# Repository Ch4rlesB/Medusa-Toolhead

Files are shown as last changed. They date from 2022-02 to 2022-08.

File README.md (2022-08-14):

# Medusa-Toolhead
**__IN BETA 3__**
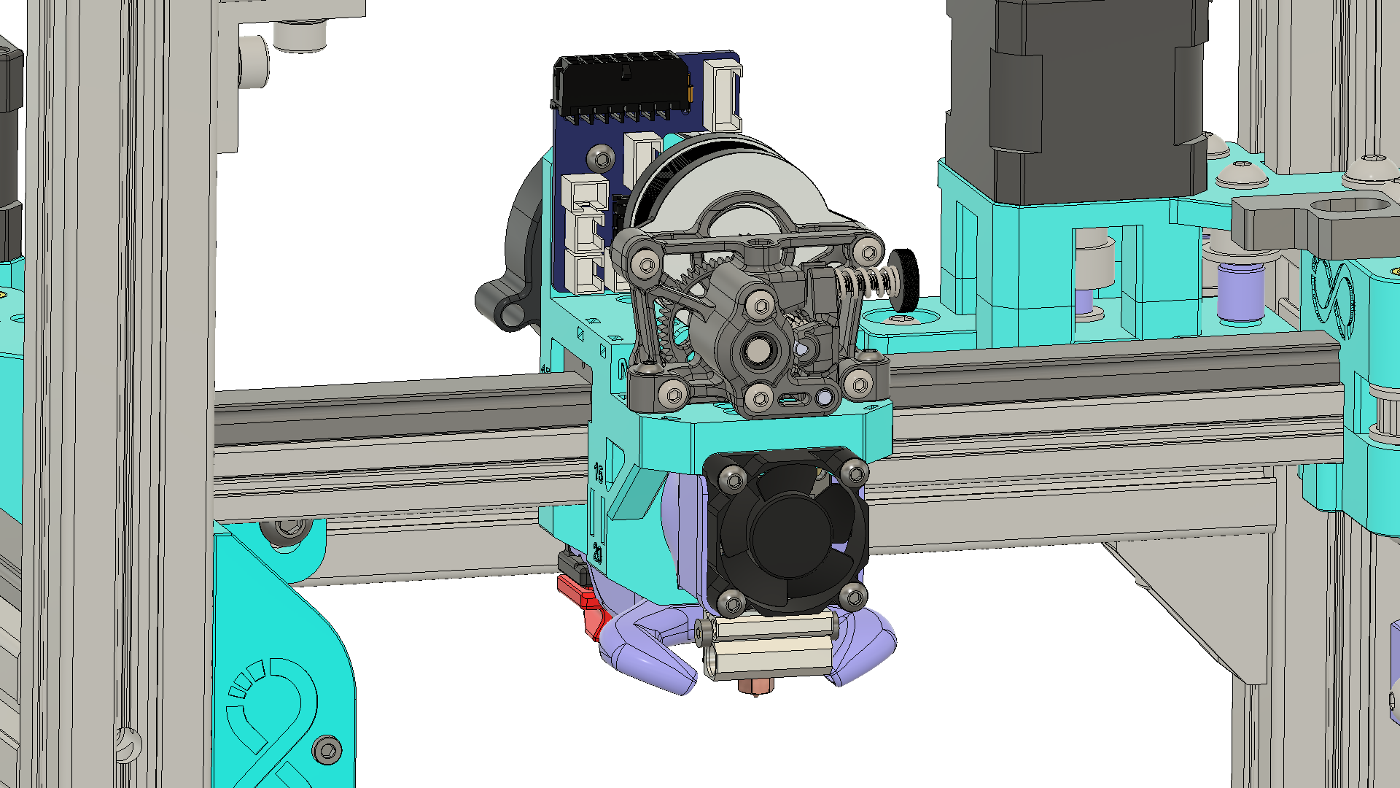
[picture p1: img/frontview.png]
FrontView


**Beta 3 Changelog:**
- Removed the slide in belt attachment method. You now loop around a post and ziptie the belt to itself, à la VZBot. (Pardon my french)

- Much Much MUCH stiffer. Horizontal bar that holds extruder and hotend does not flex at all now.

- Removed compability for the BLTouch as it is too unreliable inside a 60C enclosure.

- Narrowed down the Umbilical options to:

	I. Straight umbilical with strain relief.

	II. Hartk Afterburner Toolhead board. (ALOT of different wiring            harnesses on aliexpress made to work with this board that                facilitate 		   wiring overall)

- Standardized the screw sizes.

- CFD work to align the airflow from the duct better.

# **__What is it?__**

EVA 2.4 replacement for the [**SnakeOil-XY CoreXY 3D Printer**](https://github.com/ChipCE/SnakeOil-XY).

Designed to need the least hardware possible while still being stiff and light.

## **1. Toolhead**

### 1.1 Currently supports:

	Extruder:
	-Sherpa Mini Extruder
	
	Hotend:
	- Dragon SF and HF
	- Mosquito or NF-Crazy
	
	Probe:
	- Klicky Probe

	Umbilical:
	- Hartk Voron 2.4 Toolhead board
	- Normal umbilical
  Toolhead Board            |  No Toolhead Board
:-------------------------:|:-------------------------:
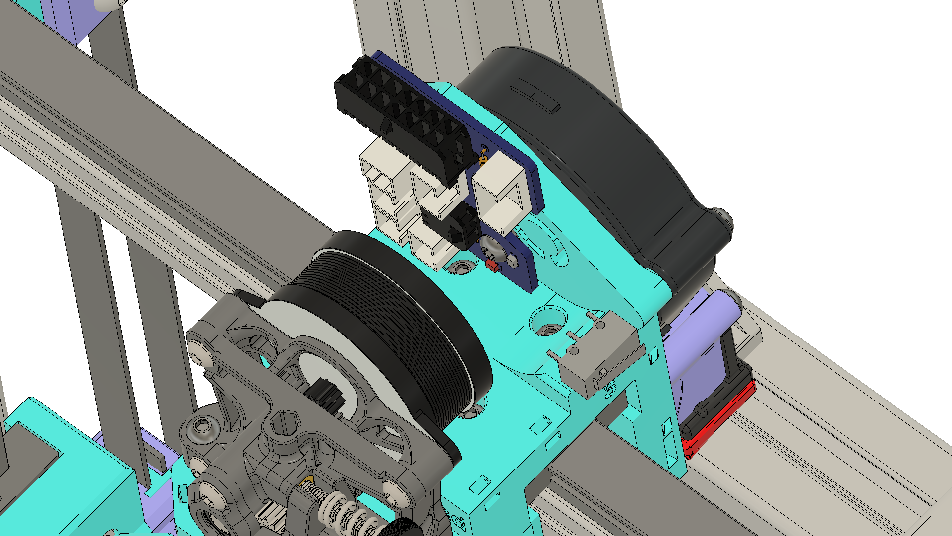
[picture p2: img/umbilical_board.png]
umbilical_board
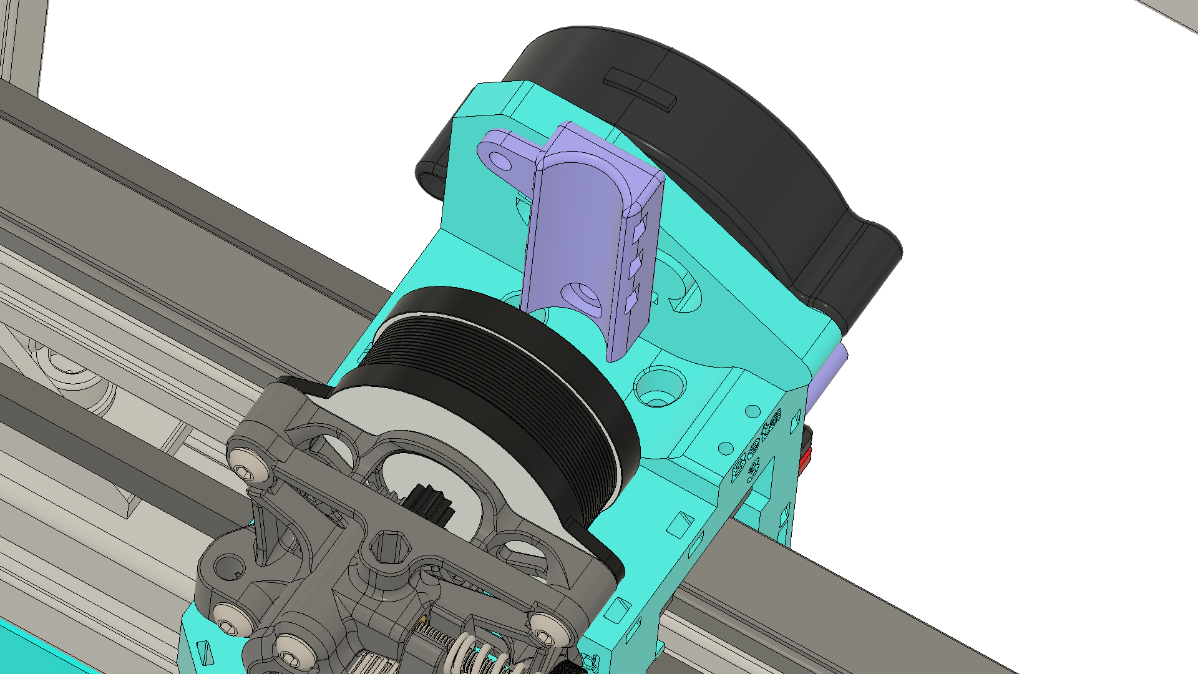
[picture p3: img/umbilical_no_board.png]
umbilical_no_board
  |  

### 1.2 Cooling 
Uses a modified [Eva](https://github.com/EVA-3D/eva-main) cooling duct.
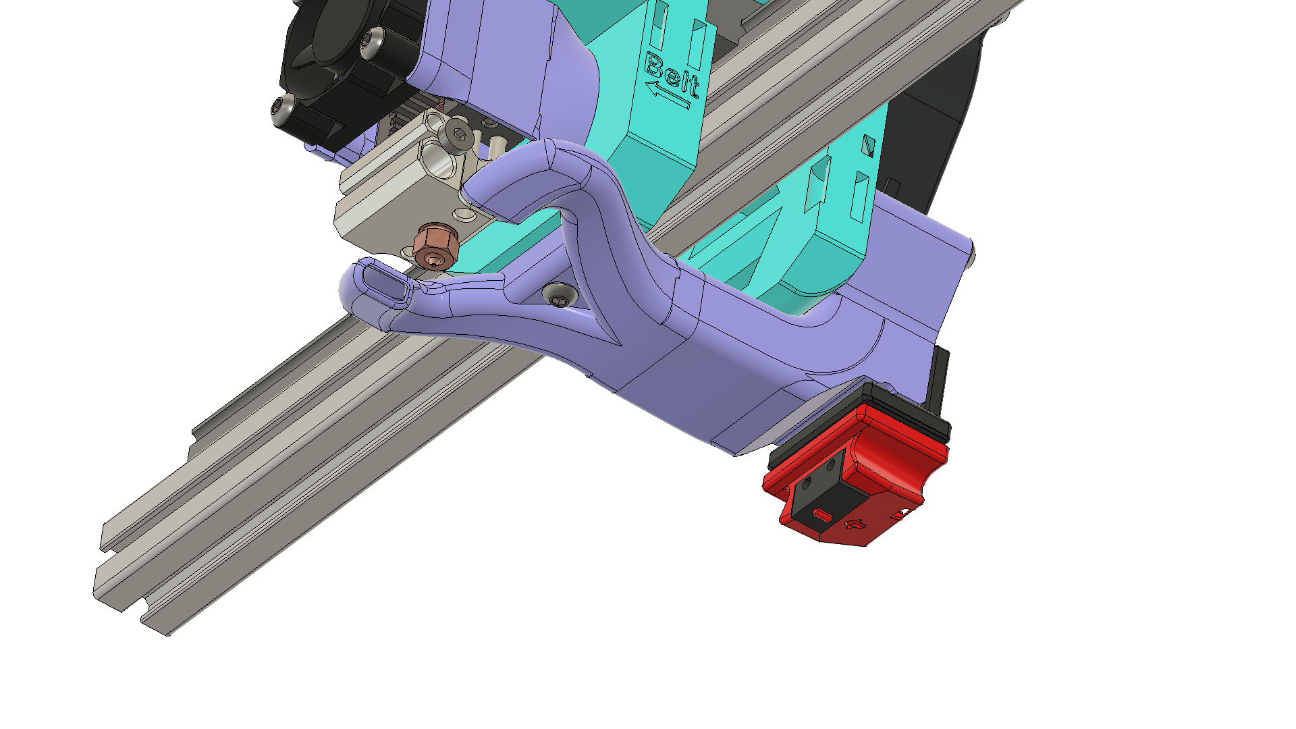
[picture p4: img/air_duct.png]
Air Duct

### 1.3 Offsets
	 x : -1.8 mm
	 y : 76.85 mm
	 z : 6.2 mm
### 1.4 BOM
	- 1x Dragon OR Mosquito (NF-Crazy) Hotend

	- 1x Fully Assembled Sherpa Mini Extruder

	- 1x 3010 Fan for hotend cooling.
	
	- 1x 5015 Fan for part cooling

	- 6x M3-6mm Screw (MGN12, Umbilical)

	- 7x M3-12mm Screw (Hotend Cooling Fan, Shroud, Cooling Duct, Sherpa mini mounting)

	- 3x M3-25mm Screw (Cooling Duct and Fan) 

	- Mounting hardware that goes with your hotend (Usually 2 or 4 M2.5 screws)

	- 2x M2x10mm self tapping screws (Endstop mounting)

	- 14x M3 Heatset insert M3x4mmx4mm

	- OPTIONAL 1x hartk afterburner toolhead board

	- 4x Zipties (Belts)
						AND
	- Klicky
		- 2x M3-6mm Screw
		- 2x M3-16mm Screws
		- 2x M2-10mm self tapping screws
		- 2x M6-8mm Screw
		- 2x M3 Heatset insert M3x4mmx4mm
		- 1x Omron D2F Microswitch or similar
		- 8x 6x3mm round magnets
		
### Assembly

ToolheadAssembly

## **2. Tensioning Idlers**

Belt mounting on the toolhead itself is very simplified to save weight. You will need to print the tensioning front idlers and replace the static stock ones. This will allow you to tension the belts.

Front            |  Back
:-------------------------:|:-------------------------:
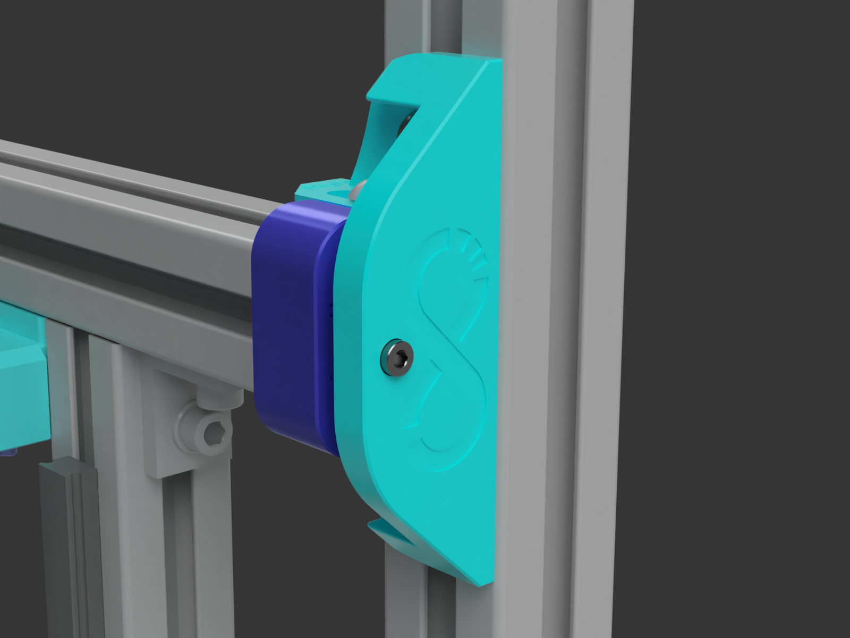
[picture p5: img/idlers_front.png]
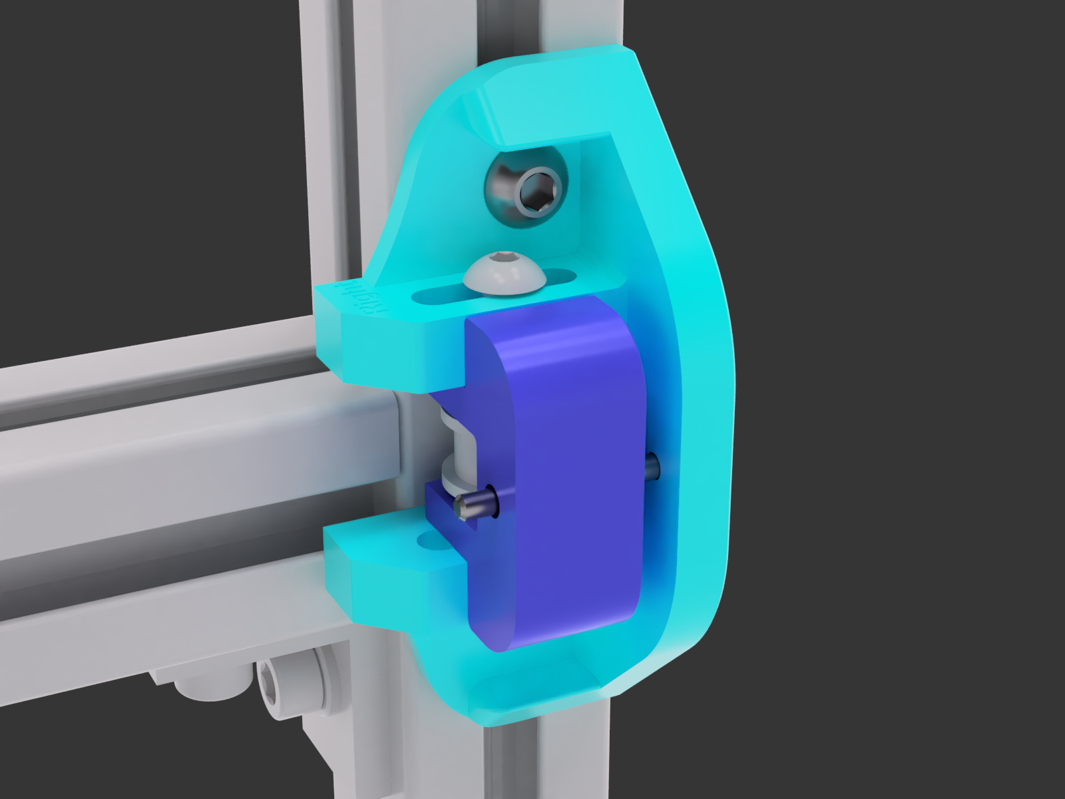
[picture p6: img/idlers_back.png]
  |  

### Bom
	- 2x M5x40mm Button Head (Idler shaft)
	- 2x M5 Standard Nut (Idler shaft)
	- 4x M6x8mm (Mouting the idlers to the frame - Reuse the ones used to hold the old idlers in place)
	- 2x M3x30mm Button Head (Tensioning Screw)
	- 12x M3 Heatset insert M3x4mmx4mm

## **3. Klicky Probe**
 Currently supports [Klicky probe](https://github.com/jlas1/Klicky-Probe) with a custom toolhead mount and dock mount.

Toolhead Mount            |  Dock & Mount
:-------------------------:|:-------------------------:
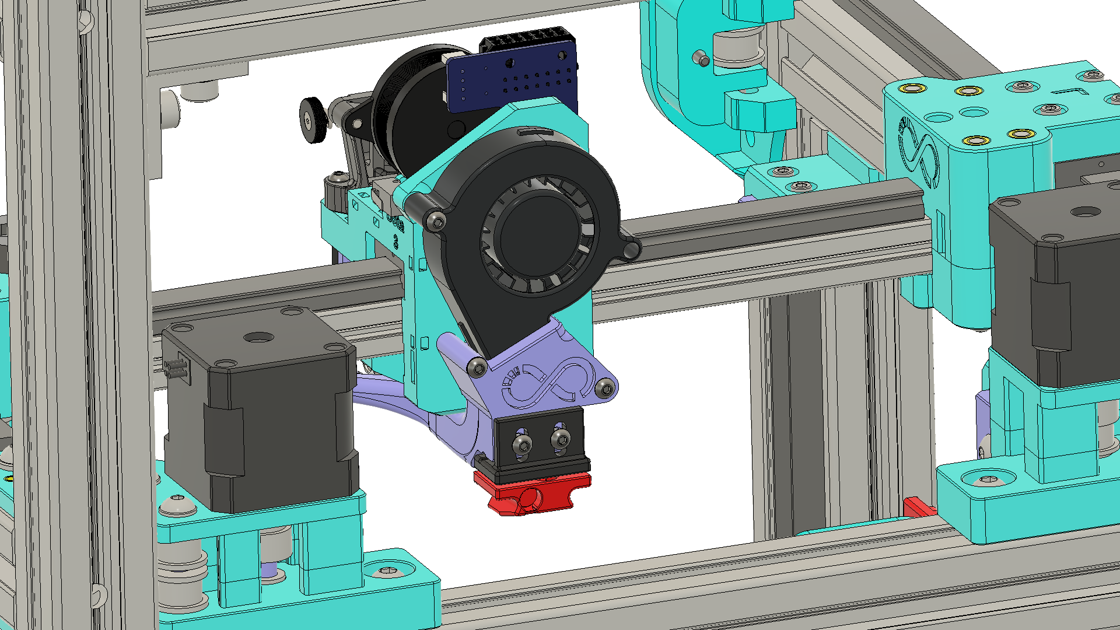
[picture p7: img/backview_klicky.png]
backview_klicky
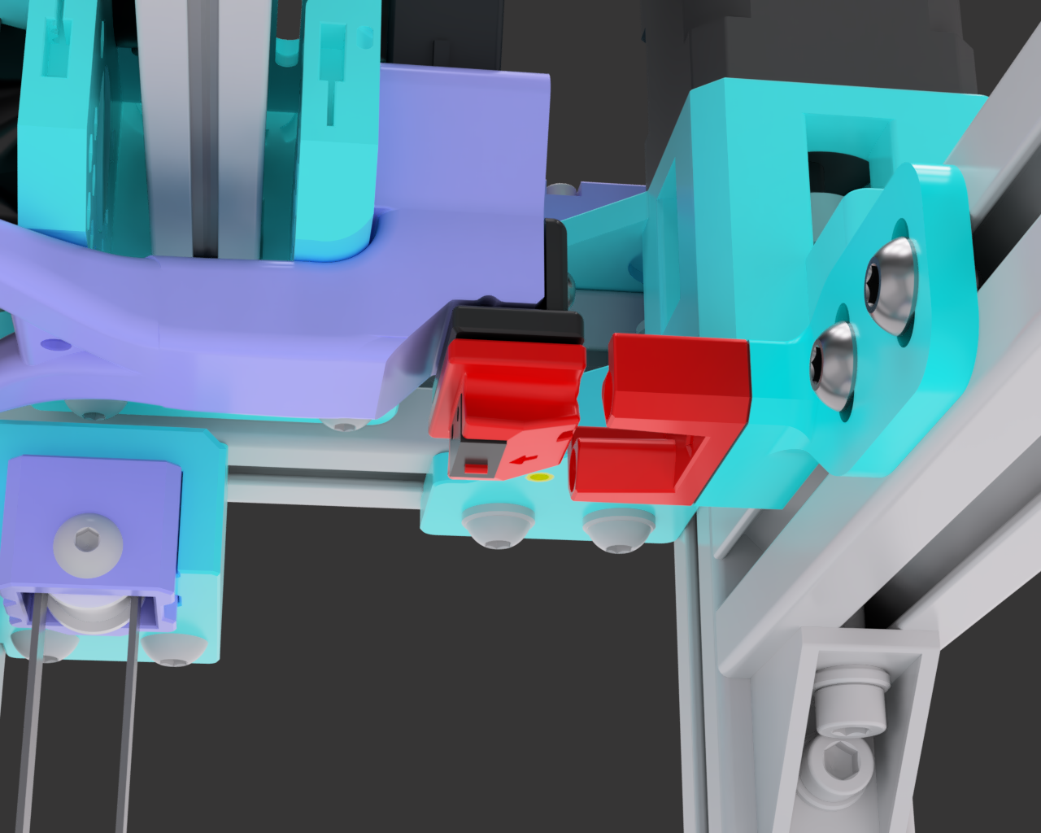
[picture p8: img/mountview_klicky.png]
mount_klicky
  |  

## **4. Z Endstop**
 Based on the Z endstop present on [Voron 3D Printers](https://github.com/VoronDesign).

 Acts as your z endstop and lets you use the [Z Calibration tool](https://github.com/protoloft/klipper_z_calibration) in conjunction with the Klicky Probe, to automatically set your Z offset independently of nozzle or print surface.

SnakeOil modified version            |  Based on the [Voron](https://docs.vorondesign.com/community/howto/120decibell/z_endstop_configuration.html) z endstop
:-------------------------:|:-------------------------:
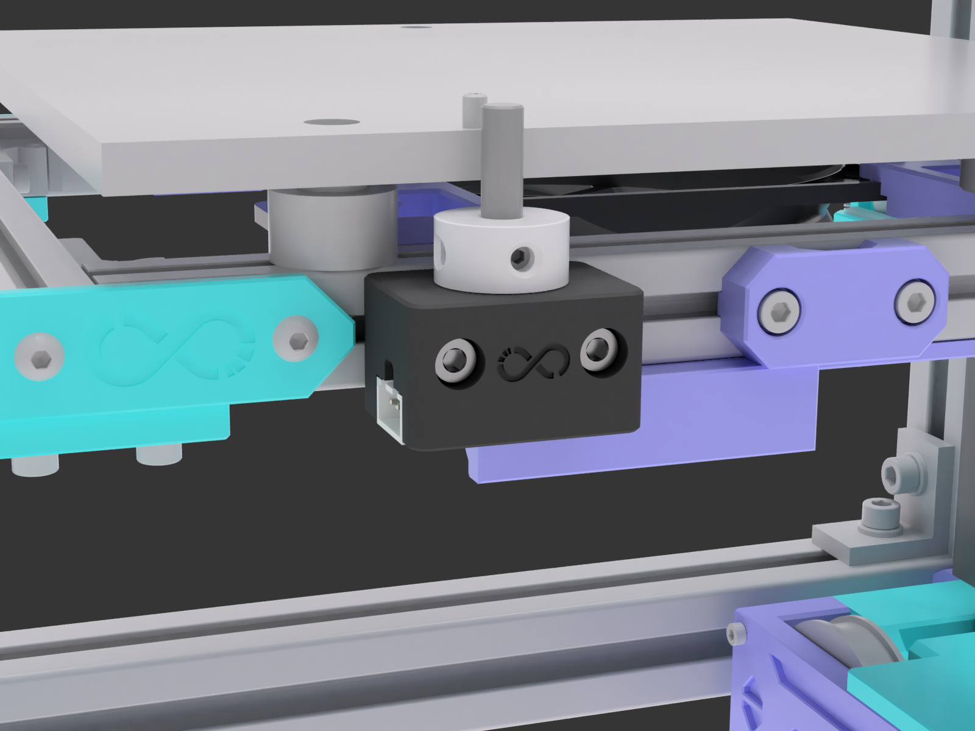
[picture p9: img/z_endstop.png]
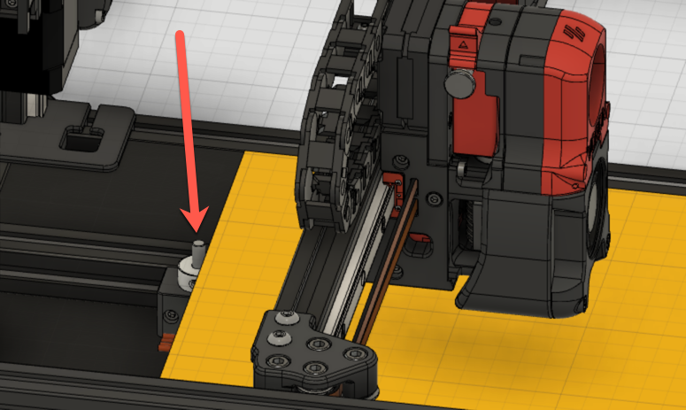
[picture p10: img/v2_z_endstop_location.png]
  |  

### Bom
	-2x M3x2mm Button Head (Mounting to bed)
	-2x M3 Standard Nut (Mounting to bed)
	-1x 5mm x 25mm Steel shaft
	-1x Omron D2F Microswitch or similar
	-1x 20-tooth timing pulley (deflanged)

 If you are having trouble taking the flange off the pulley visit the [version 2.2](https://github.com/VoronDesign/Voron-2/tree/Voron2.2/STLs/VORON2.2/Tools) of the Voron repository under tools. After printing out the hub puller and using the bolts from the kit, de-flanging is very easy.

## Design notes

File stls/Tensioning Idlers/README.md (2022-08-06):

If the part has this at the end of its name:
- <code> _1 </code> -> print 1

- <code> _a </code> -> print with your accent color

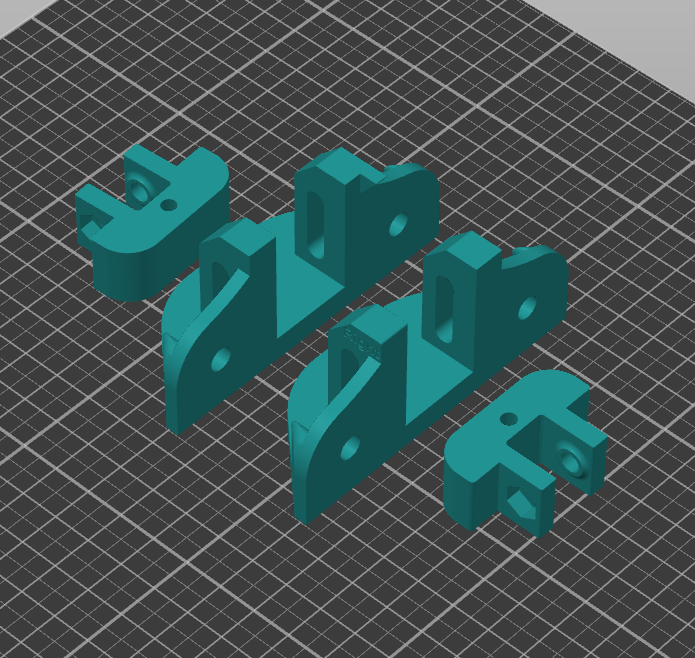
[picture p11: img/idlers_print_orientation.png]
PrintOrientation


When installing, make sure the idlers are at right height to keep belts parallel.

	- No need for support. 
	- 3-4 Perimeters
	- 30-40% Infill

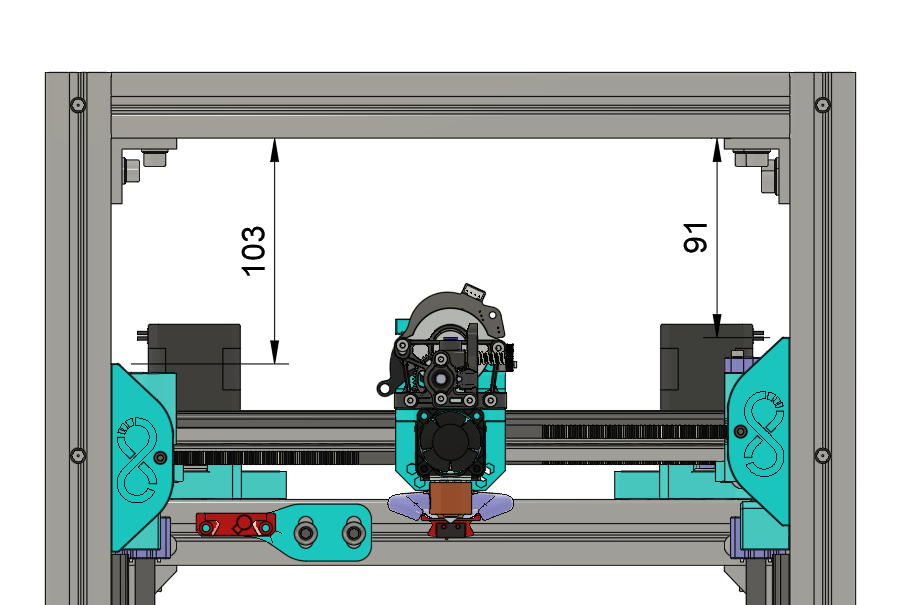
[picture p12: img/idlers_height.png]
IdlersHeight


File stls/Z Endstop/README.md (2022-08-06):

If the part has this at the end of its name:
- <code> _1 </code> -> print 1

- <code> _a </code> -> print with your accent color

	- No need for support. 
	- 3-4 Perimeters
	- 30-40% Infill

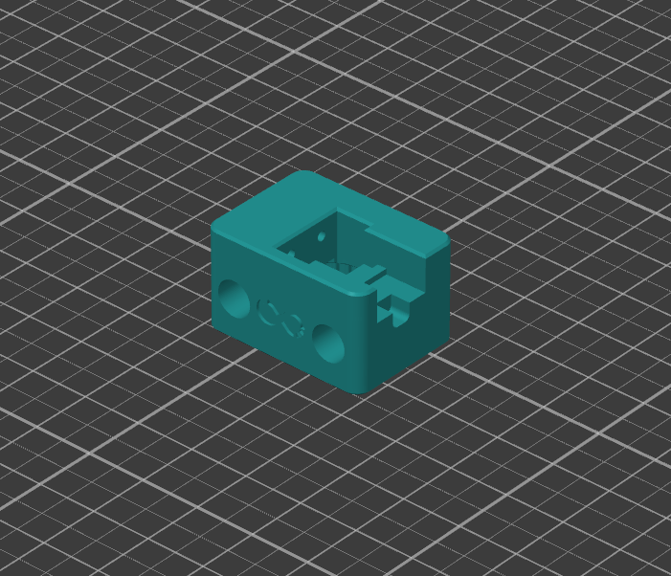
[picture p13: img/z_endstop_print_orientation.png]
PrintOrientation


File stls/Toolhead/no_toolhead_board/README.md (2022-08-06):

If the part has this at the end of its name:
- <code> _1 </code> -> print 1

- <code> _2 </code> -> print 2

- <code> _a </code> -> print with your accent color

	- No need for support. 
	- 3-4 Perimeters
	- 30-40% Infill

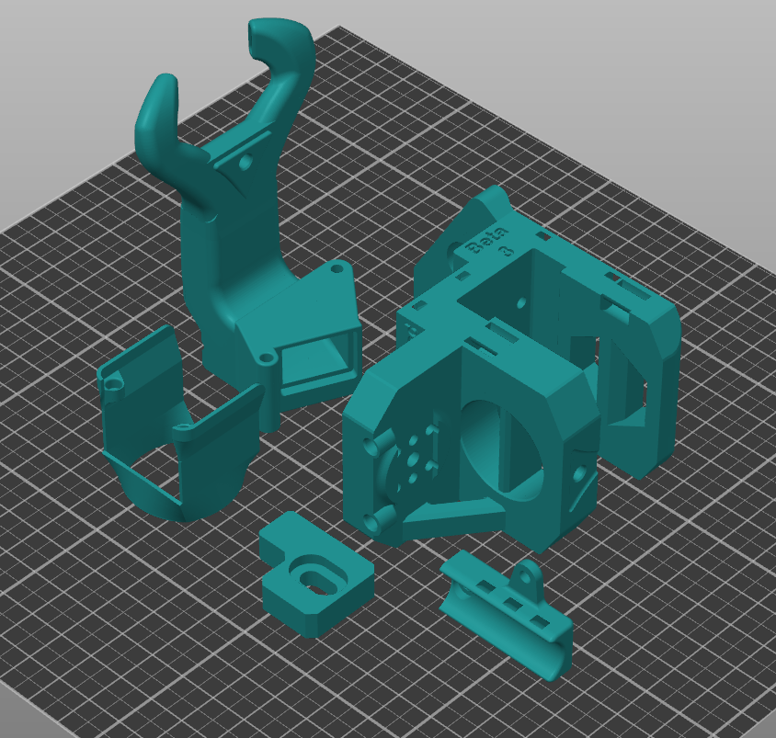
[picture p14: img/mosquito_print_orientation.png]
PrintOrientation


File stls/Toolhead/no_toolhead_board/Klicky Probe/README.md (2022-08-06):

If the part has this at the end of its name:
- <code> _1 </code> -> print 1

- <code> _2 </code> -> print 2

- <code> _a </code> -> print with your accent color

	- No need for support. 
	- 3-4 Perimeters
	- 30-40% Infill

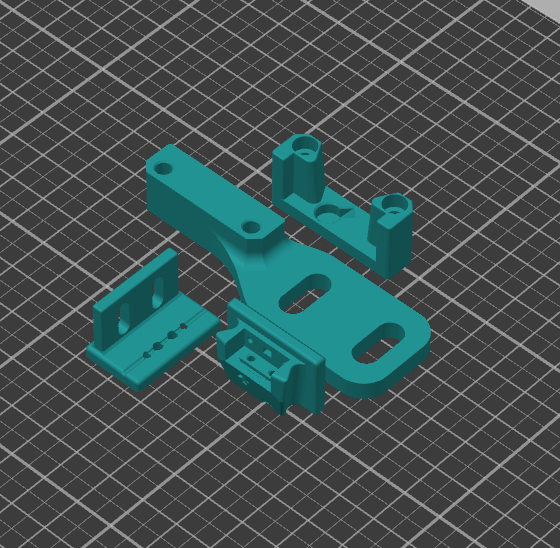
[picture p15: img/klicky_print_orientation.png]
PrintOrientation


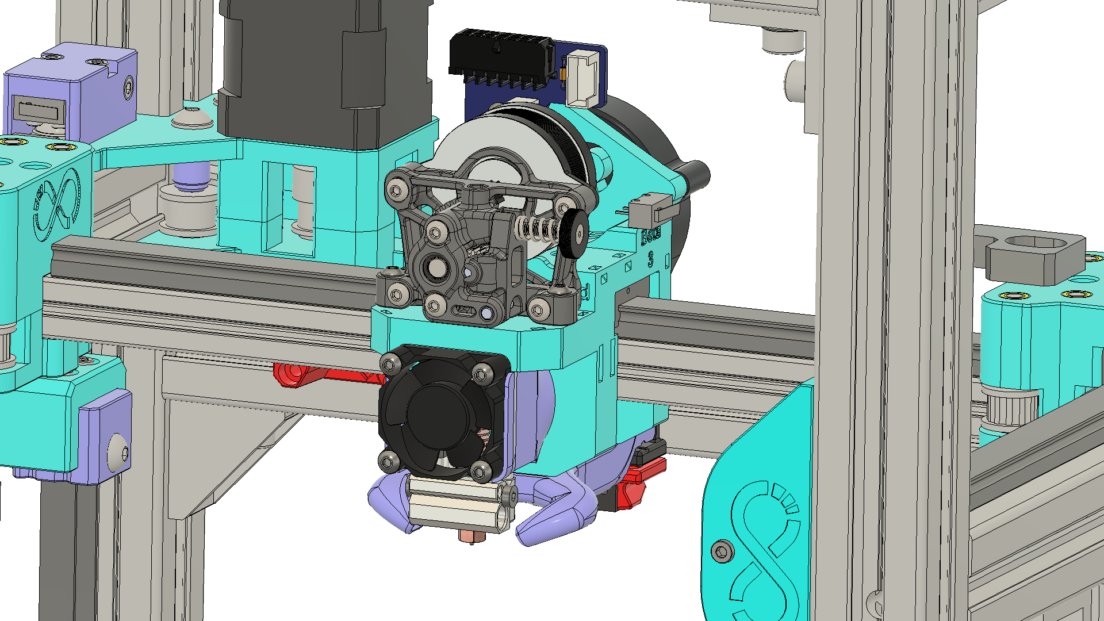
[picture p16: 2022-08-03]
img/frontview_klicky.png

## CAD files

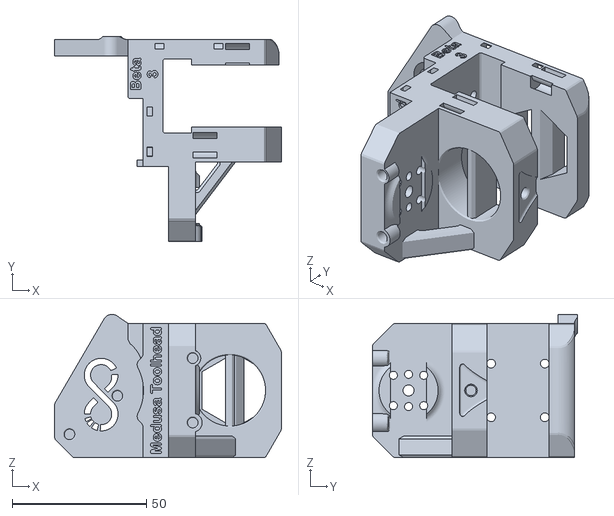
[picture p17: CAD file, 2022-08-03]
stls/Toolhead/no_toolhead_board/main_body_1.stl
84.6 x 76.5 x 53.3

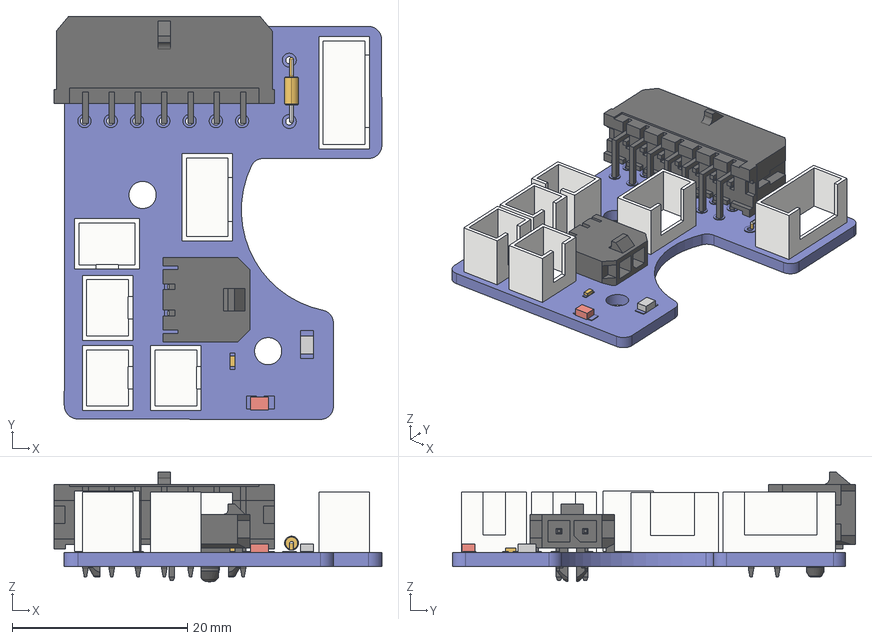
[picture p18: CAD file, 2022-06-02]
CAD/reference models/Toolhead pcb V2.4.step
37.4 x 46.0 x 12.5 mm
PCB (1)
CHAMBER THERMISTOR
RESISTOR
LED
ABL
STEPPER
XENDSTOP
BAT85
HEFAN
PCFAN
TH1
Microfit14
Microfit2

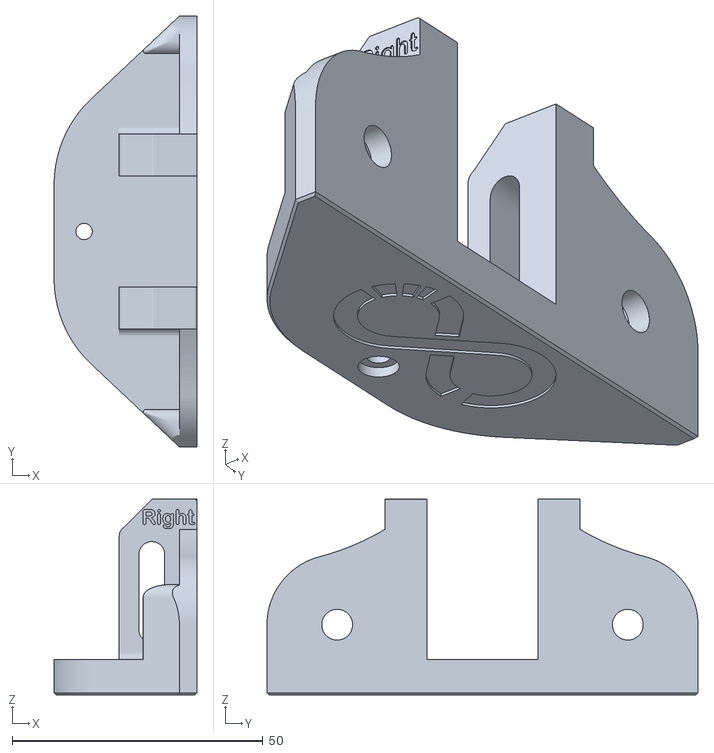
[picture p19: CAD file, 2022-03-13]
stls/Tensioning Idlers/outer_right_1.stl
28.5 x 86.0 x 39.0

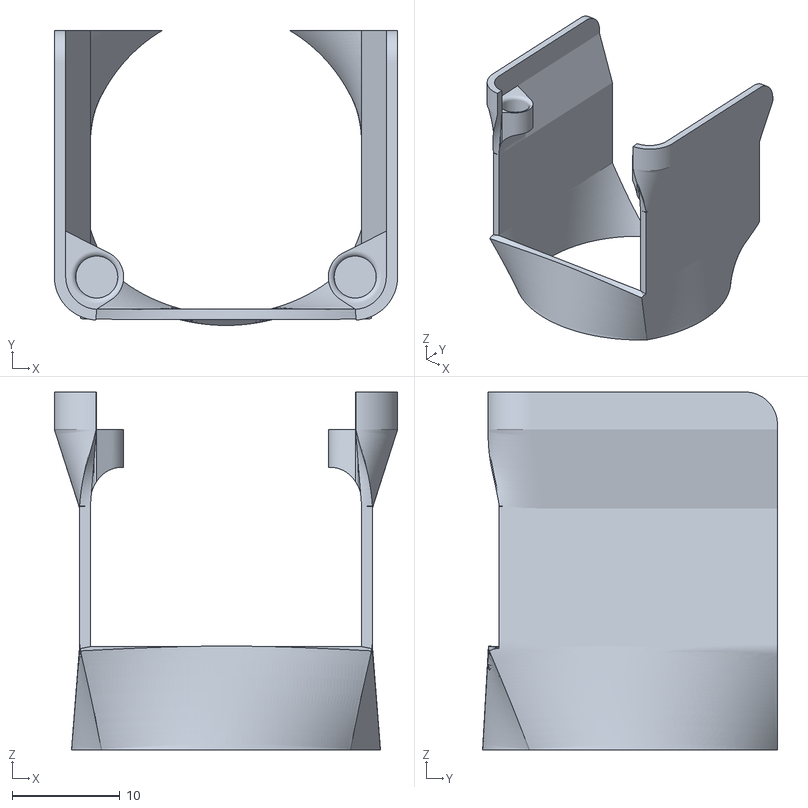
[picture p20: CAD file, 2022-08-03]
stls/Toolhead/no_toolhead_board/cooling_shroud_mosquito_a_1.stl
31.9 x 27.4 x 33.2

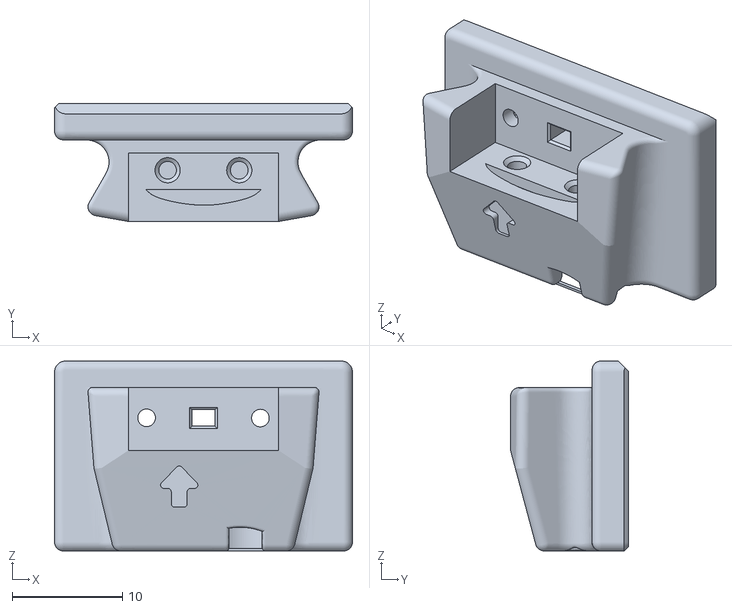
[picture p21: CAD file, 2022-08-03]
stls/Toolhead/no_toolhead_board/Klicky Probe/klicky_probe_body_a_1.stl
27.0 x 10.7 x 17.2

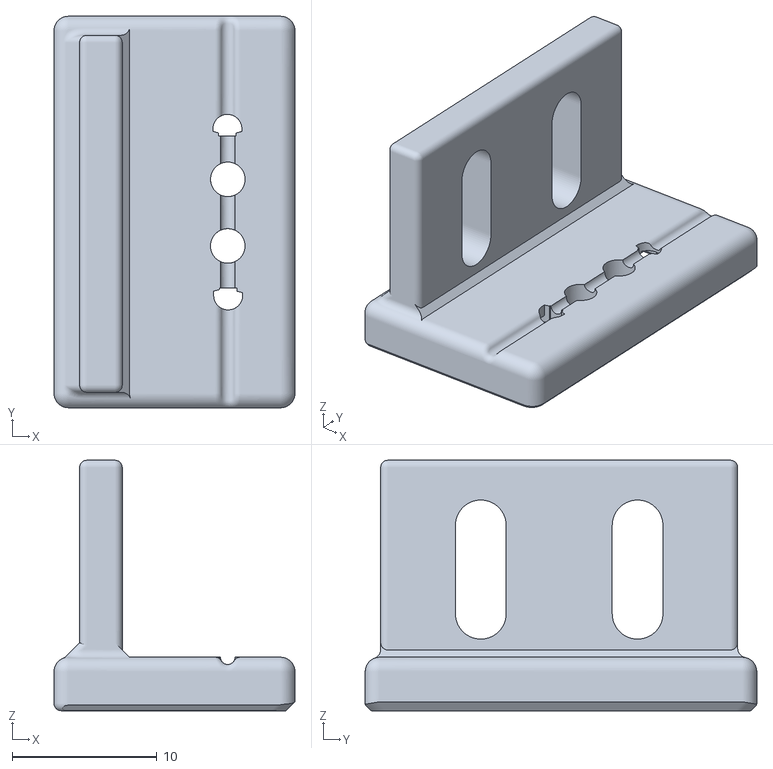
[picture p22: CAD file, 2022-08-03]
stls/Toolhead/toolhead_board/Klicky Probe/klicky_probe_mount_toolhead_1.stl
16.6 x 27.0 x 17.3

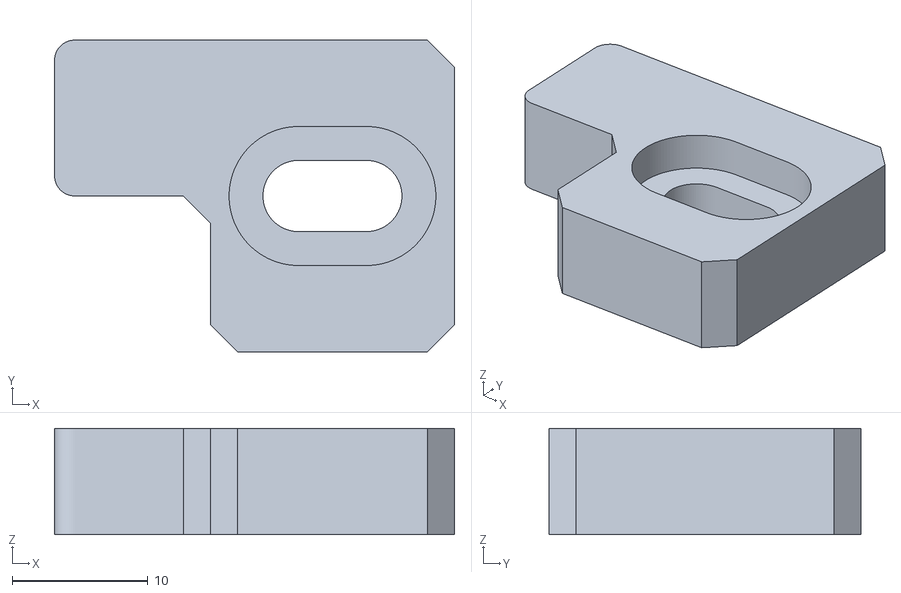
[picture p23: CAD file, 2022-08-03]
stls/Toolhead/toolhead_board/x_endstop_flag_a_1.stl
29.5 x 23.0 x 7.85

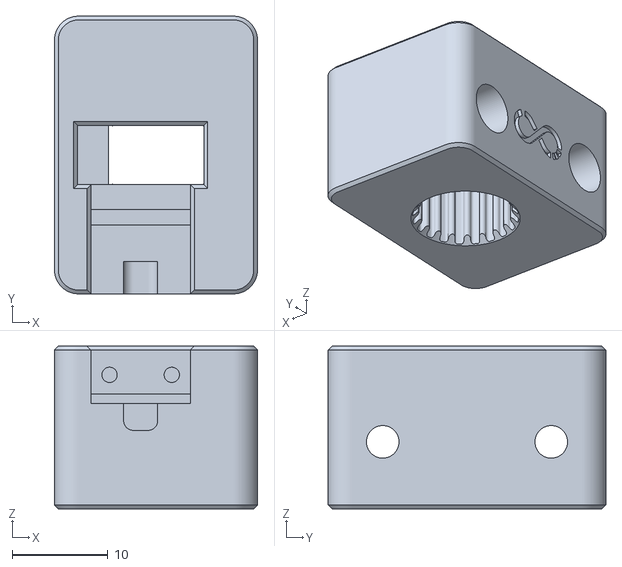
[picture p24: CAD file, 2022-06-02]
stls/Z Endstop/z_endstop_body_a_1.stl
21.2 x 29.0 x 17.0

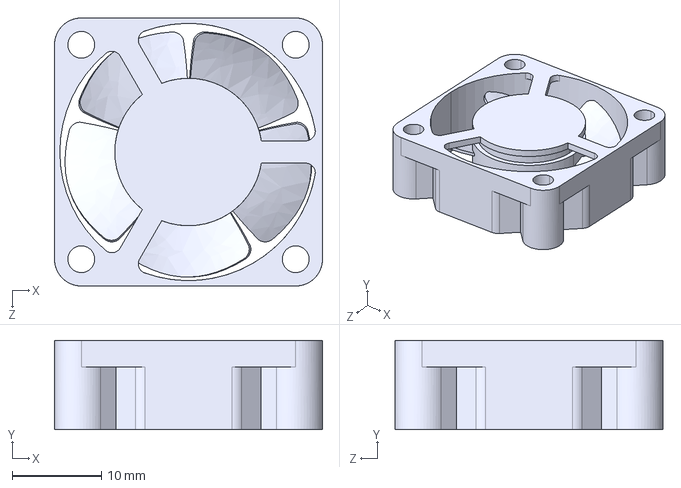
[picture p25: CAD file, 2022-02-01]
CAD/reference models/3010 HotEnd Fan.STEP
30.0 x 10.0 x 30.0 mm

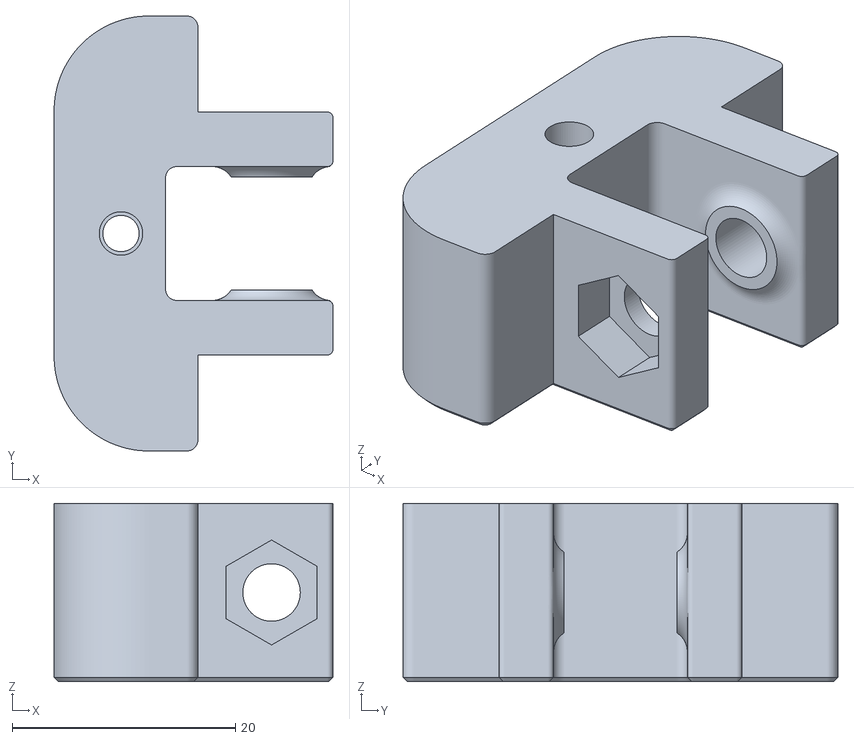
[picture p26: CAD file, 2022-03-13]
stls/Tensioning Idlers/inner_left_1_a.stl
25.0 x 39.0 x 16.0

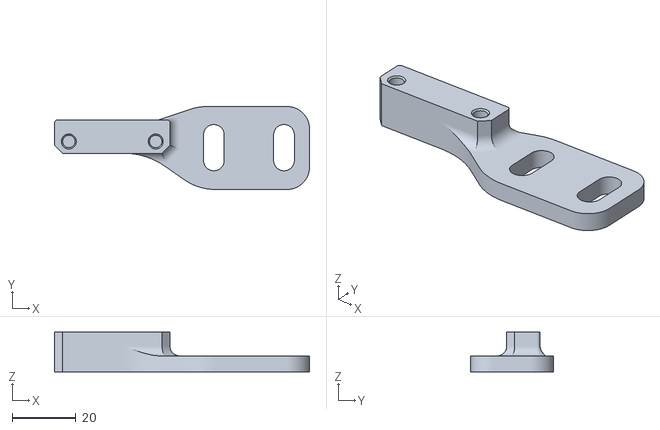
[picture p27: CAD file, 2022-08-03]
stls/Toolhead/no_toolhead_board/Klicky Probe/klicky_probe_mount_frame_lower_1.stl
80.0 x 26.0 x 12.4

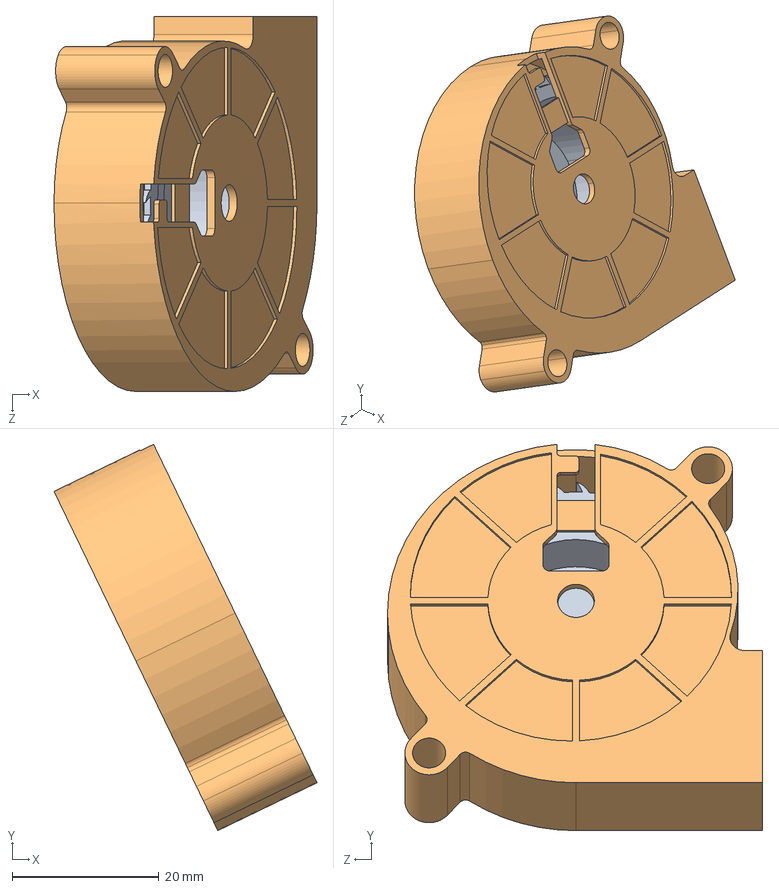
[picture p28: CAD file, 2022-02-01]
CAD/reference models/5015 Sunon Blower Fan.STEP
35.8 x 52.6 x 51.1 mm

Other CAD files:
stls/Tensioning Idlers/inner_right_1_a.stl
CAD/reference models/mosquito_model_to_publish.STEP
stls/Tensioning Idlers/outer_left_1.stl
stls/Toolhead/no_toolhead_board/Klicky Probe/klicky_probe_mount_frame_upper_1.stl
stls/Toolhead/no_toolhead_board/umbilical_no_toolhead_board_a_1.stl
stls/Toolhead/toolhead_board/Klicky Probe/klicky_probe_mount_frame_upper_1.stl

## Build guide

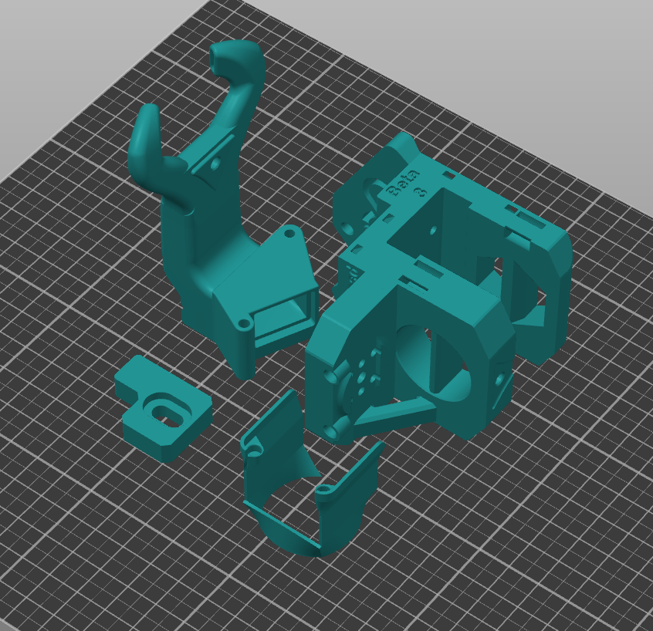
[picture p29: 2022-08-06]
img/mosquito_toolboard_print_orientation.png

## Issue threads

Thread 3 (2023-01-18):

The belt dose not parallel to X-axis

yiutoto, 2023-01-18:
Hello！

The belt from medusa does not parallel to the x-axis linear rail and so that the back side of the belt should scrub the window of y-axis rail mount and may affect the print size.

This issue comes from the difference of distance from x-axis rail; the window of y-axis rail mount: 7-10.5mm, and the outside of the belt window of medusa: 13.5mm (left side of back), 12mm (right side of back).

What do you think about this? I think that this issue can be solved by moving the position of x-axis rail mount and the surrounding parts, and also extending the area to fix the belt.

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

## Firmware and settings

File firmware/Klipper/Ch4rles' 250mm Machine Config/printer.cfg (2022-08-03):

# Gcode and custom macros
[include macro.cfg]
#[include adxl.cfg]

[virtual_sdcard]
path: ~/gcode_files

[pause_resume]
recover_velocity: 50


[display_status]

[idle_timeout]
timeout: 7200

[mcu]
# USB
serial: /dev/serial/by-id/usb-Klipper_stm32f446xx_300023001350324E31333220-if00
#UART
#serial: /dev/ttyAMA0
#restart_method: command

[force_move]
enable_force_move: True

[printer]
kinematics: corexy
max_velocity: 450 
max_accel: 15000
max_accel_to_decel: 15000
max_z_velocity: 24
max_z_accel: 240
square_corner_velocity: 6

#####################################################################
#      X/Y Stepper Settings
#####################################################################


# motor 0 port
[stepper_x]
step_pin: PF13
dir_pin: !PF12
enable_pin: !PF14
microsteps: 16
rotation_distance: 40
full_steps_per_rotation:200
endstop_pin: !PG6
#endstop_pin: !PG9
position_endstop: 248
position_max: 248
position_min : -1
homing_speed: 50

[tmc2209 stepper_x]
uart_pin: PC4
run_current: 1.1
#hold_current: 0.500
sense_resistor: 0.110
interpolate: true
stealthchop_threshold: 0


# motor 1 port
[stepper_y]
step_pin: PG0
dir_pin: !PG1
enable_pin: !PF15
microsteps: 16
rotation_distance: 40
full_steps_per_rotation:200
#endstop_pin: !PG6
endstop_pin: !PG9
position_endstop: 250
position_max: 250
position_min : -8
homing_speed: 50

[tmc2209 stepper_y]
uart_pin: PD11
run_current: 1.1
#hold_current: 0.500
sense_resistor: 0.110
interpolate: true
stealthchop_threshold: 0


# motor 2 port
#[stepper_unused1]
#step_pin: PF11
#dir_pin: PG3
#enable_pin: !PG5
#microsteps: 16
#rotation_distance: 8
#endstop_pin: PG10
#position_endstop: 0
#position_max: 200
#homing_speed: 12
#second_homing_speed: 1

#[tmc2209 stepper_unused1]
#uart_pin: PC6
#interpolate: true
#run_current: 0.800
#hold_current: 0.500
#stealthchop_threshold: 0


#####################################################################
#   Extruder
#####################################################################

# motor 3 port
[extruder]
step_pin: PG4
dir_pin: !PC1
enable_pin: !PA0
rotation_distance: 22.67895 #for 5mm Shaft Driven Bondtech gearsets
#gear_ratio: 50:10 #for standard 10t motor
gear_ratio: 50:8 #for sherpa mini 8t motor
microsteps: 16
full_steps_per_rotation: 200
nozzle_diameter: 0.400
filament_diameter: 1.750
max_extrude_only_distance: 1400.0
max_extrude_only_velocity: 75.0
max_extrude_only_accel: 1500
min_temp: 0
max_temp: 385
max_power: 1.0
min_extrude_temp: 20
smooth_time: 2.0
heater_pin: PA2 # HE3
sensor_type: Generic 3950
sensor_pin: PF3
pressure_advance = 0.044
#control: pid
#pid_Kp: 22.2
#pid_Ki: 1.08
#pid_Kd: 114

[tmc2209 extruder]
uart_pin: PC7
run_current: 0.35
#hold_current: 0.150
sense_resistor: 0.110
interpolate: true
stealthchop_threshold: 0




# motor 4 port
#[stepper_unused2]
#step_pin: PF9
#dir_pin: PF10
#enable_pin: !PG2
#microsteps: 16
#rotation_distance: 8
#endstop_pin: PG10
#position_endstop: 0
#position_max: 200
#homing_speed: 12
#second_homing_speed: 1

#[tmc2209 stepper_unused2]
#uart_pin: PF2
#interpolate: true
#run_current: 0.800
#hold_current: 0.500
#stealthchop_threshold: 0


#####################################################################
#   Z Stepper Settings
#####################################################################

# motor 5 port
[stepper_z]
step_pin: PC13
dir_pin: PF0
enable_pin: !PF1
rotation_distance: 40
gear_ratio: 80:16
microsteps: 16
full_steps_per_rotation:200 
endstop_pin: !PG10
position_endstop: -1.25
position_max: 210
position_min: -10
homing_speed: 10
second_homing_speed: 3
homing_retract_dist: 3

[tmc2209 stepper_z]
uart_pin: PE4
run_current: 0.600
hold_current: 0.450
sense_resistor: 0.110
interpolate: true
stealthchop_threshold: 0


# motor 6 port
[stepper_z1]
step_pin: PE2
dir_pin: !PE3
enable_pin: !PD4
rotation_distance: 40
gear_ratio: 80:16
microsteps: 16
full_steps_per_rotation:200 

[tmc2209 stepper_z1]
uart_pin: PE1
run_current: 0.600
hold_current: 0.450
sense_resistor: 0.110
interpolate: true
stealthchop_threshold: 0




# motor 7 port
[stepper_z2]
step_pin: PE6
dir_pin: !PA14
enable_pin: !PE0
rotation_distance: 40
gear_ratio: 80:16
microsteps: 16
full_steps_per_rotation:200 

[tmc2209 stepper_z2]
uart_pin: PD3
run_current: 0.600
hold_current: 0.450
sense_resistor: 0.110
interpolate: true
stealthchop_threshold: 0


#####################################################################
#	Probe
#####################################################################

[probe]
##	Inductive Probe - If you use this section , please comment the [bltouch] section
##	This probe is not used for Z height, only Quad Gantry Leveling
##	In Z+ position
##	If your probe is NO instead of NC, add change pin to ^PA3
pin: PG12
x_offset: -1.783
y_offset: 75.59
z_offset: 6.9 #2.5
speed:4
lift_speed: 8.0
samples: 3
samples_result: median
sample_retract_dist: 1.25
samples_tolerance: 0.01 #0.007
samples_tolerance_retries: 5

[z_calibration]
nozzle_xy_position: 200,249
#   A X, Y coordinate (e.g. 100,100) of the nozzle, clicking on the Z endstop.
switch_xy_position: 200,172
#   A X, Y coordinate (e.g. 100,100) of the probe's switch body, clicking on
#   the Z endstop.
bed_xy_position: 125,125
#   a X, Y coordinate (e.g. 100,100) where the print surface (e.g. the center
#   point) is probed. These coordinates will be adapted by the
#   probe's X and Y offsets. The default is the relative_reference_index
#   of the configured bed_mesh, if configured. It's possible to change the relative
#   reference index at runtime or use the GCode argument BED_POSITION of CALIBRATE_Z.
switch_offset: .41
#   The trigger point offset of the used mag-probe switch.
#   Larger values will position the nozzle closer to the bed.
#   This needs to be find out manually. More on this later
#   in this section..
max_deviation: 2
#   The maximum allowed deviation of the calculated offset.
#   If the offset exceeds this value, it will stop!
#   The default is 1.0 mm.
#   The calculation method when sampling more than once - either
#   "median" or "average". The default is from the probe's configuration.
clearance: 10
#   The distance in mm to move up before moving to the next
#   position. The default is two times the z_offset from the probe's
#   configuration.
#position_min: default from "stepper_z:position_min" section.
#   Minimum valid distance (in mm) used for probing move. The
#   default is from the Z rail configuration.
speed: 100
#   The moving speed in X and Y. The default is 50 mm/s.
lift_speed: 35
#   Speed (in mm/s) of the Z axis when lifting the probe between
#   samples and clearance moves. The default is from the probe's
#   configuration.
probing_speed: 4
#   The fast probing speed (in mm/s) used, when probing_first_fast
#   is activated. The default is from the Z rail configuration.
probing_second_speed: 4
#   The slower speed (in mm/s) for probing the recorded samples.
#   The default is second_homing_speed of the Z rail configuration.
probing_retract_dist: 1.5
#   Distance to retract (in mm) before probing the next sample.
#   The default is homing_retract_dist from the Z rail configuration.
probing_first_fast: true
#   If true, the first probing is done faster by the probing speed.
#   This is to get faster down and the result is not recorded as a
#   probing sample. The default is false.


[z_tilt]

# the point of the motor (or leadscrew)
z_positions:
	285, 125
	-30, 10 
	-30, 236
# probe point (nozzle) / X shift 30, y shift 5
points:
	232, 41
	23, -4
	23, 146
speed: 250
horizontal_move_z: 10
retries: 5
retry_tolerance: 0.0075

[bed_mesh]
speed: 300
horizontal_move_z: 10
##--------------------------------------------------------------------
##	Uncomment below for 250mm build
mesh_min: 10, 80
mesh_max: 240,180
##--------------------------------------------------------------------
fade_start: 0.6
fade_end: 10.0
probe_count: 5,5
algorithm: bicubic
relative_reference_index: 12

#####################################################################
#   Bed Heater
#####################################################################

[heater_bed]
heater_pin: PA1
sensor_pin: PF4 # T3
sensor_type: Generic 3950
#control: pid
min_temp: 0
max_temp: 150
max_power: 0.9
min_temp: 0
#pid_kp: 58.437
#pid_ki: 2.347
#pid_kd: 363.769

#####################################################################
#	Fan Control
#####################################################################

##	Hotend Fan --> FAN5
[heater_fan hotend_fan]
pin: PA8
max_power: 1.0
kick_start_time: 0.5
heater: extruder
heater_temp: 30.0
off_below: 0.25
fan_speed: 1

##	Part Cooling Fan --> FAN4
[fan]
pin: PE5
kick_start_time: 0.5
#off_below: 0.25

[fan_generic mcu_fan]
pin: PD15
kick_start_time: 0.5
#fan_speed: 0.3
#off_below: 0.25

[fan_generic carbon_filter]
pin: PD13
kick_start_time: 0.5
#fan_speed: 0.3
#off_below: 0.25

[delayed_gcode turnOnMCUFan]
initial_duration: 5
gcode:
  SET_FAN_SPEED FAN=mcu_fan SPEED=0.30
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

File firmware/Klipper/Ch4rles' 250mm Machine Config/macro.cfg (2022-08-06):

[homing_override]
axes: z
set_position_z: 0
gcode:
    SAVE_GCODE_STATE NAME=HOMING_state
    M117 Homing..

    
    G91                            ; relative positioning
    G0 Z10 F540                    ; move up
    G90                            ; absolute positioning

    # Home X and Y only for G28 or G28 XYZ
    {% if 'Z' in params %}
      {% if "x" not in printer.toolhead.homed_axes %}
        G28 X
      {% endif %}
      {% if "y" not in printer.toolhead.homed_axes %}
        G28 Y
      {% endif %}
    {% else %}
      G28 X Y
    {% endif %} 

    ##	XY Location of the Z Endstop Switch
    G0 X200 Y248 F12000            ; move to Z-Pin
    G28 Z                          ; home Z
    G0 Z10 F540                    ; move up

    ## return to org current/acceleration settings
    {% if params.RESET_SETTINGS|default('true') == 'true' %}
      _SET_Z_CURRENT
      _SET_ACC
    {% endif %}

    RESTORE_GCODE_STATE NAME=HOMING_state


[gcode_macro CALIBRATE_Z]
rename_existing: BASE_CALIBRATE_Z
gcode:
    _CG28 RESET_SETTINGS=false
    M117 Z-Calibration..
    SECURE_ATTACH_PROBE
    BASE_CALIBRATE_Z
    SECURE_DOCK_PROBE
    M117



[gcode_macro G32]
gcode:
    G28
    Z_TILT_ADJUST
    
    ##	Uncommentfor your size printer:
    #--------------------------------------------------------------------
    ##	Uncomment for 250mm build
    G0 X125 Y125 Z30 F3600
    
    #--------------------------------------------------------------------
[gcode_macro Z_TILT_ADJUST]
rename_existing: BASE_Z_TILT_ADJUST
gcode:
    M117 ZTA..
    G28
    _CG28 RESET_SETTINGS=false
    # reduce accel current
  
    SECURE_ATTACH_PROBE
    BASE_Z_TILT_ADJUST
    SECURE_DOCK_PROBE
    
    M117 ZTA Finished.



[gcode_macro PRINT_START]
#   Use PRINT_START for the slicer starting script - please customise for your slicer of choice
variable_parameter_EXTRUDER_TEMP: 190
variable_parameter_BED_TEMP: 60
; gcode parameters for area bed mesh
variable_parameter_AREA_START : 0,0
variable_parameter_AREA_END : 0,0
gcode:


    {% if not printer.z_tilt.applied %}
        M117 Z Tilt adjusting...
        Z_TILT_ADJUST
        
    {% endif %}
    G28 Z
    #BED_MESH_CALIBRATE AREA_START={params.AREA_START|default("0,0")} AREA_END={params.AREA_END|default("0,0")}
    CALIBRATE_Z
    G1 Z20 F3000                   ; move nozzle away from bed 
    G1 X125 Y125 F5000

[gcode_macro PRINT_END]
#   Use PRINT_END for the slicer ending script - please customise for your slicer of choice
gcode:
    M400                           ; wait for buffer to clear
    G92 E0                         ; zero the extruder
    G1 E-2.0 F3600                ; retract filament
    G91                            ; relative positioning
    G0 Z1.00 X20.0 Y20.0 F20000    ; move nozzle to remove stringing
    TURN_OFF_HEATERS
    BED_MESH_CLEAR
    M107                           ; turn off fan
    G1 Z2 F3000                    ; move nozzle up 2mm
    G90                            ; absolute positioning
    G0  X125 Y240 F3600            ; park nozzle at rear
    
[gcode_macro PAUSE]
rename_existing: BASE_PAUSE
# change this if you need more or less extrusion
variable_extrude: 1.0
gcode:
  ##### read E from pause macro #####
  {% set E = printer["gcode_macro PAUSE"].extrude|float %}
  ##### set park positon for x and y #####
  # default is your max posion from your printer.cfg
  {% set x_park = printer.toolhead.axis_maximum.x|float - 5.0 %}
  {% set y_park = printer.toolhead.axis_maximum.y|float - 5.0 %}
  ##### calculate save lift position #####
  {% set max_z = printer.toolhead.axis_maximum.z|float %}
  {% set act_z = printer.toolhead.position.z|float %}
  {% if act_z < (max_z - 2.0) %}
      {% set z_safe = 2.0 %}
  {% else %}
      {% set z_safe = max_z - act_z %}
  {% endif %}
  ##### end of definitions #####
  SAVE_GCODE_STATE NAME=PAUSE_state
  BASE_PAUSE
  G91
  G1 E-{E} F2100
  G1 Z{z_safe} F900
  G90
  G1 X{x_park} Y{y_park} F6000
  
[gcode_macro RESUME]
rename_existing: BASE_RESUME
gcode:
  ##### read E from pause macro #####
  {% set E = printer["gcode_macro PAUSE"].extrude|float %}
  ##### end of definitions #####
  G91
  G1 E{E} F2100
  RESTORE_GCODE_STATE NAME=PAUSE_state
  BASE_RESUME

[gcode_macro CANCEL_PRINT]
rename_existing: BASE_CANCEL_PRINT
gcode:
  ##TURN_OFF_HEATERS
  CLEAR_PAUSE
  SDCARD_RESET_FILE
  BASE_CANCEL_PRINT  

[gcode_macro SECURE_ATTACH_PROBE]
gcode:
    QUERY_PROBE
    _PROBE_ACTION action=attach
    _CHECK_PROBE action=check_attach

# docking the probe if not already docked
[gcode_macro SECURE_DOCK_PROBE]
gcode:
    QUERY_PROBE
    _PROBE_ACTION action=dock
    _CHECK_PROBE action=check_dock


[gcode_macro _CHECK_PROBE]
variable_probe_state: 0
gcode:
    QUERY_PROBE
    _PROBE_ACTION action={ ACTION }

[gcode_macro _PROBE_ACTION]
  
gcode:
  {% set state = not printer.probe.last_query %}
  SET_GCODE_VARIABLE MACRO=_CHECK_PROBE VARIABLE=probe_state VALUE={ state }

  # attach/dock probe
  {% if not state and params.ACTION == 'attach' %}
    _ATTACH_PROBE
  {% endif %}
  {% if state and params.ACTION == 'dock' %}
    _DOCK_PROBE
  {% endif %}

  # check if probe fails to attach/detach
  {% if state and params.ACTION == 'check_dock' %}
    { action_raise_error("Probe dock failed!") }
  {% endif %}
  {% if not state and params.ACTION == 'check_attach' %}
    { action_raise_error("Probe attach failed!") }
  {% endif %}

# this attaching from above is more silent but would
# be dangerous if the probe is already attached!
#[gcode_macro _ATTACH_PROBE]
#gcode:
#    SAVE_GCODE_STATE NAME=_ATTACH_PROBE
#    SET_GCODE_OFFSET Z=0.0         ; reset offset - will be restored
#    G90                            ; absolute positioning
#    G0 X252.5 Y300 Z10 F12000      ; move to mag-probe
#    G0 Z0.0 F540                   ; move down to mag-probe
#    G0 Y285 F6000                  ; move out
#    G0 Z10 F540                    ; move up
#    RESTORE_GCODE_STATE NAME=_ATTACH_PROBE

[gcode_macro _ATTACH_PROBE]
gcode:
    SAVE_GCODE_STATE NAME=_ATTACH_PROBE
    SET_GCODE_OFFSET Z=0.0        ; reset offset - will be restored
    G90   
    G0 Z30  F600                ; absolute positioning
    G0 X10 Y236 F6000          ; move to mag-probe
    G0 Y250 F4000                 ; move in
    G0 Y236 F4000                 ; move out
    RESTORE_GCODE_STATE NAME=_ATTACH_PROBE

[gcode_macro _DOCK_PROBE]
gcode:
    SAVE_GCODE_STATE NAME=_DOCK_PROBE
    SET_GCODE_OFFSET Z=0.0        ; reset offset - will be restored
    G90                           ;absolute positioning
    G0 Z30 F540                   ;move to Z
    G0 X9.8 Y230 F12000             ; move to mag-probe
    G0 Y250 F5000                 ; move in
    G0 X45 F4000                  ; move right
    G0 Y236 F4000                   ; move back
    RESTORE_GCODE_STATE NAME=_DOCK_PROBE

[gcode_macro PROBE_ACCURACY]
rename_existing: _PROBE_ACCURACY
gcode:
    #store current nozzle location
    #SAVE_GCODE_STATE NAME=original_nozzle_location
    SECURE_ATTACH_PROBE
    PARKCENTER Z={printer.configfile.settings.z_tilt_adjust.horizontal_move_z}
    _PROBE_ACCURACY {% for p in params 
            %}{'%s=%s' % (p, params[p])}{% 
           endfor %}
    SECURE_DOCK_PROBE
    #restore current nozzle location
    #RESTORE_GCODE_STATE NAME=original_nozzle_location MOVE=1
[gcode_macro LOAD_FILAMENT]
gcode:
   M83                            ; set extruder to relative
   G1 E30 F300                    ; load
   G1 E15 F150                    ; prime nozzle with filament
   M82                            ; set extruder to absolute
    
[gcode_macro UNLOAD_FILAMENT]
gcode:
   M83                            ; set extruder to relative
   G1 E10 F300                    ; extrude a little to soften tip
   G1 E-40 F1800                  ; retract some, but not too much or it will jam
   M82                            ; set extruder to absolute
[gcode_macro BED_MESH_CALIBRATE]
rename_existing:             _BED_MESH_CALIBRATE
gcode:
    
    CheckProbe action=query
    SECURE_ATTACH_PROBE

    _BED_MESH_CALIBRATE 

    SECURE_DOCK_PROBE
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

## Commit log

2022-02-01 Initial stl and step commit
    [3010 HotEnd Fan.STEP, 5015 Sunon Blower Fan.STEP, Inner Left x1.3mf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]
2022-02-03 added dragon shroud
    [Shroud Dragon.3mf, Shroud Mosquitto.3mf, bltouch_mount.3mf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]
2022-02-03 Modified Idlers geometry to aid in printability
    [Inner Left x1.3mf, Inner Right x1.3mf, Outer x2.3mf]
2022-02-11 Updated main_body
    [Shroud Dragon.3mf, Shroud Mosquitto.3mf, main_body.3mf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]
2022-02-11 Update README.md
    Removed umbilical mount text
2022-02-17 Added Clicky Probe Support
    [Dock Mount.stl, Dock.stl, Probe Toolhead Mount.stl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]
2022-02-17 removed dupe folders
    [Shroud Dragon.3mf, Shroud Mosquitto.3mf, bltouch_mount.3mf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]
2022-02-17 Fixed Klicky Names
    [Dock Mount.stl, Dock.stl, Probe Toolhead Mount.stl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]
2022-02-21 Fixed Dragon 1.5mm offset were ducts would collide with print bed
    [Cooling Duct Klicky.step, Cooling Duct_BlTouch.step, main_body.stl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]
2022-02-21 Added Full Cad
    [Cooling Duct Klicky.step, Cooling Duct_BlTouch.step]
2022-02-21 added alt cooling ducts and shrouds
2022-02-23 Modified parts to help with cable management
    [Probe Toolhead Mount.stl, cooling_duct_klicky.stl]
2022-02-24 Removed 3mf files and replaced with orientated stls in idler section
    [Inner Left x1.3mf, Inner Left x1.stl, Inner Right x1.3mf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]
2022-03-01 Moved print orientation images to /img and updated readmes.
2022-03-01 Naming convention
    [bltouch_mount_x1.stl, cooling_duct_klicky_x1_a.stl, cooling_duct_x1_a.stl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]
2022-03-01 Updated BOM
2022-03-03 Modified idlers to add strenght and positioning
    [inner_left_x1_a.stl, inner_right_x1_a.stl, outer_left_x1.stl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]
2022-03-13 Added MiniAB Support
    [inner_left_x1_a.stl, inner_right_x1_a.stl, outer_left_x1.stl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]
2022-03-15 added strain relief for mini AB version
    [bltouch_mount_x1.stl, cooling_duct_klicky_x1_a.stl, cooling_duct_x1_a.stl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]
2022-03-24 Updated the CAD
2022-05-26 Added Voron Toolhead PCB support
2022-06-02 Added Z endstop and reformated first page
    [Klicky Mount.step, Toolhead pcb V2.4.step, Z Endstop Assembly.step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]
2022-08-03 Modified text, images and cad for Beta 3
    [Klicky Mount.step, Z Endstop Assembly.step]
2022-08-03 updated STLS for Beta3
    [bltouch_mount_x1.stl, cooling_duct_klicky_x1_a.stl, cooling_duct_x1_a.stl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]
2022-08-06 Updated print orientations and naming scheme. Final Beta 3 Release
    [cooling_shroud_mosquito_a_1.stl, inner_left_1_a.stl, inner_right_1_a.stl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]
2022-08-06 Add files via upload
    Added air duct image
2022-08-14 Added assembly gif
